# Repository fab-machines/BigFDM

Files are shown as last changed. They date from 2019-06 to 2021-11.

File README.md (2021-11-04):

<div align="center"><h1 style="font-family: courier;" align="center">BigFDM</h1></div>

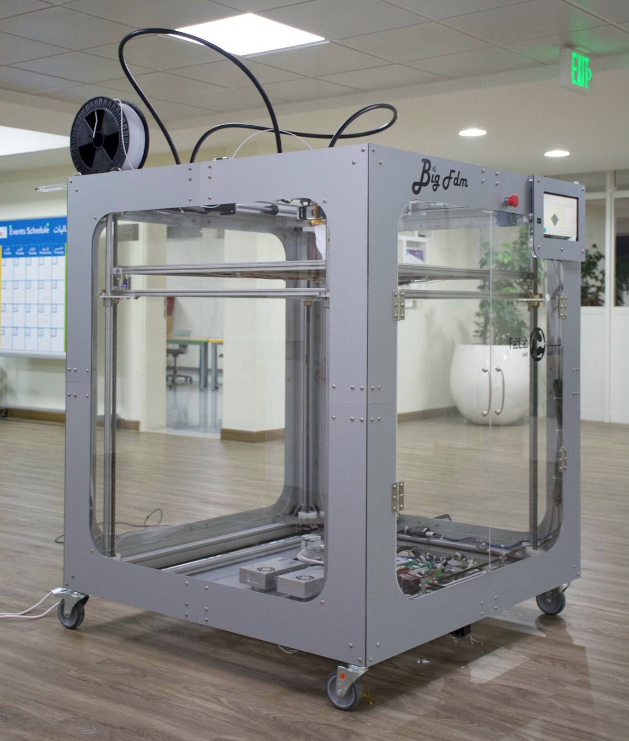
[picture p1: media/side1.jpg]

<div align="center"><i>Open Source Large Scale 3D Printer</i></div>

Premises
--
We dream in a future of freedom, where open source hardware and [Fab Labs](https://fablabs.io/) enable people to fully understand how to make things they need, and where decentralized local production is customized to impact the surrounding community. Believing that empowering the user with knowledge about how to make machines, BigFDM wants to give to the world a powerful open source tool, to 3D print any large scale object you may need. And, together with [LaserDuo](http://laserduo.com/), this is one of the first steps in developing other machines sharing the same philosophy.

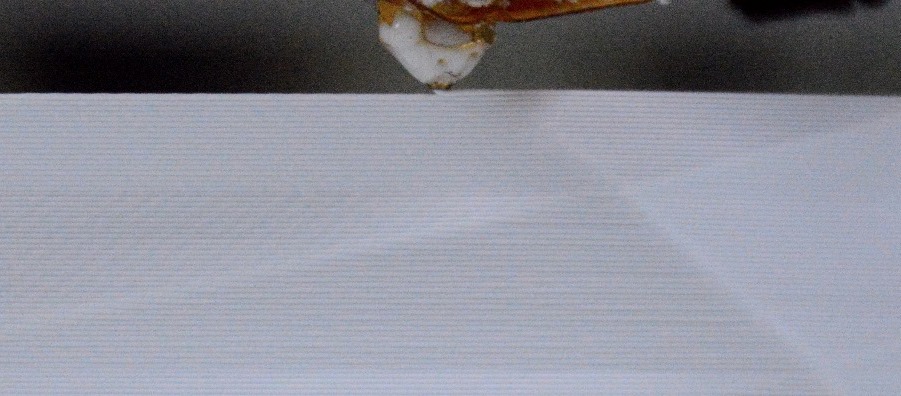
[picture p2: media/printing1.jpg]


BigFDM
--
BigFDM is an open source large scale 3D printer. 

Taking advantage of what we have learned in [Fab Academy](https://fabacademy.org/), BigFDM has been developed using standard [Fab Lab equipment](https://docs.google.com/spreadsheets/d/1U-jcBWOJEjBT5A0N84IUubtcHKMEMtndQPLCkZCkVsU/pub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) and [techniques](http://fab.academany.org/2019/schedule.html). BigFDM was in fact built in [Fab Lab UAE](http://fablabuae.ae/) by Daniele Ingrassia with the help of Hashim Al Sakkaf. Reversing the consumer process, where knowledge and building of machines stays inside a black box managed by companies, BigFDM brings the advantages of an open source development:

- full awareness about how the machine works
- reproducible design
- possibility to customize the machine and/or to build new ones
- built as much as possible with local materials
- local self-fixing and self-production of the machine parts
- community can use and improve the design
- cheap alternative to large scale 3D printers
- use BigFDM as tool to produce other open source machines

BigFDM allows the printing of large scale objects, some examples can be orthotics and prosthesis, art installations, furniture, replacement parts, industrial design prototypes, molds for casting of full scale parts. Using  Fused Deposition Modeling (or FDM), it can use standard 2.85mm 3D printer filament, and as well common extruders nozzles.

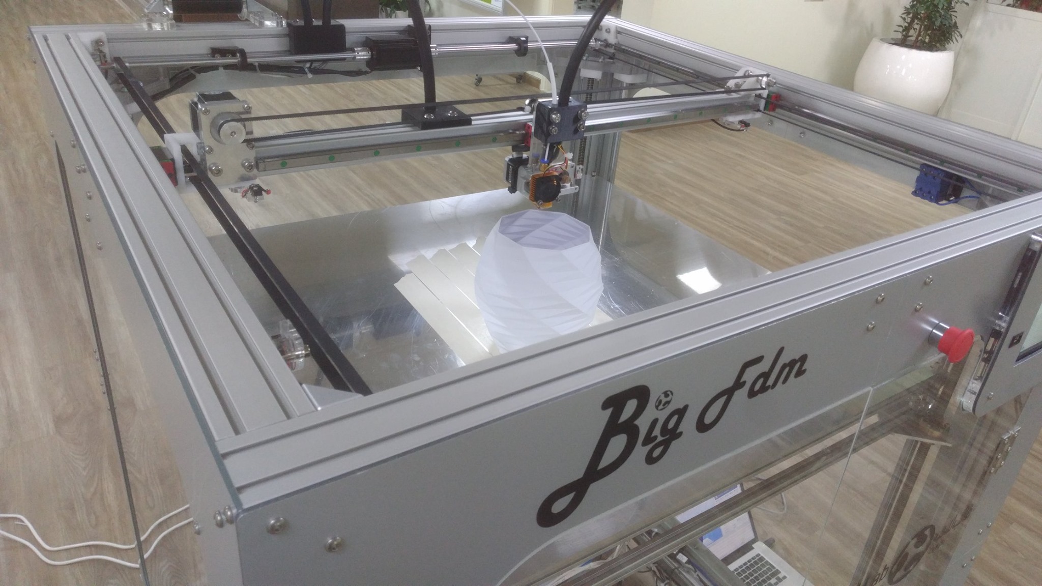
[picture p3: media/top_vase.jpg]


**BigFDM specifications**:

- **800mm x 800mm x 900mm** printing area
- **dual extruder** with interchangeble nozzle
- **2.85mm** filament
- **0.4 - 1mm** nozzle size
- **NEMA 24/23**  stepper motors
- stages with **HiWin linear guides**
- anodized **aluminium frame**
- **heated bed** with 4 x 750W bed heaters
- **closed housing** of aluminum composite and acrylic
- fabbable **[satshakit](https://github.com/satshakit) and [satstep](https://github.com/satstep)** based electronics
- **integrated tablet** for machine control
- printing from **USB** drive
- BOM cost of about **2600€**
- power requirements 220V, 3000W max

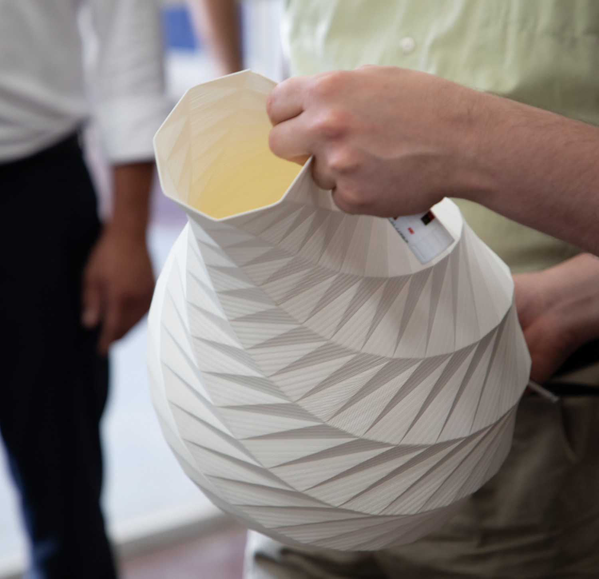
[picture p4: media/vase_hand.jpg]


Machine design
--
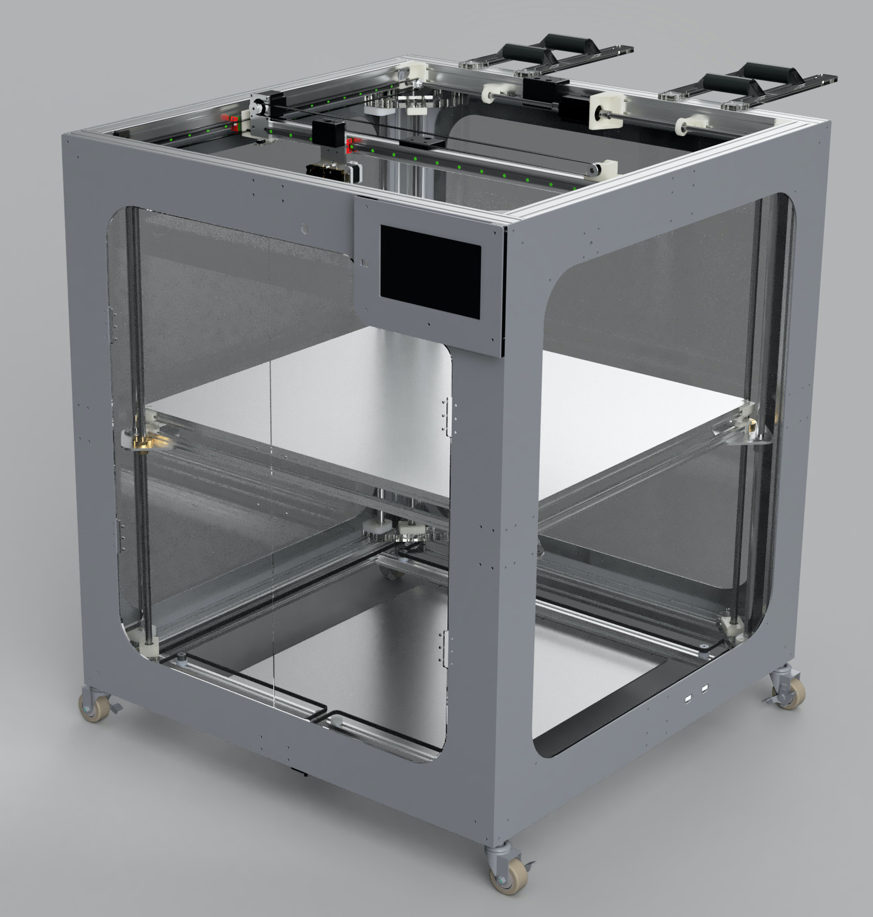
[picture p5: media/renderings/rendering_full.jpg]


BigFDM has been designed considering to keep fixed from the beginning few constraints, which then influenced the rest of the subsequent design choices:

- the all machine parts must be inside a boxed main frame
- the machine XY stages design must be independent and consistent by itself
- the Z axis moves the bed up or down

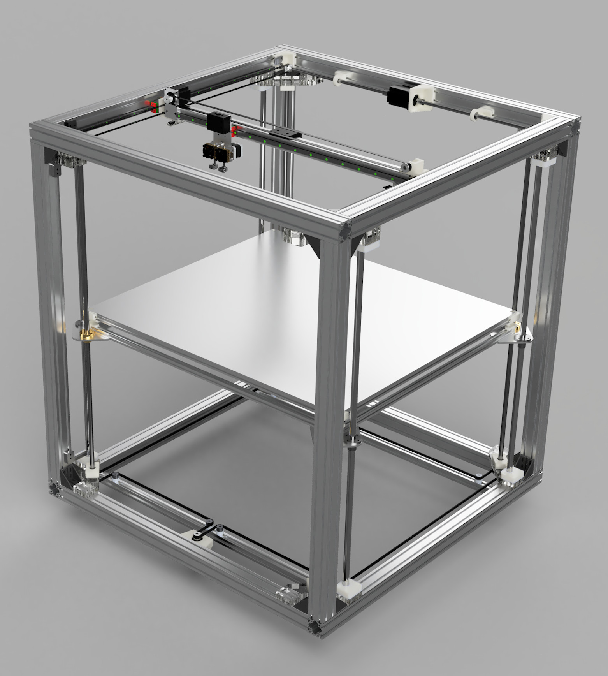
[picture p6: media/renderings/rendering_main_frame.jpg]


These have been tought in order to bring the following benefits:

- a **compact design** that maximize the printing area while minizing the unused space (just 2mm between the bed supports and the housing!)
-  minimizing the unused space has **lowered the cost** of the frame and the housing parts
-  the main frame serves both as **structural squared reference** for all the machine parts and well as body for the housing
-  the **XY stages can be completely removed** without disassembling any other machine section
-  the **XY stage indipendent design** can be reused to develop other machines
-  the machine printing **area can be scaled up/down** just by changing the length of few machine parts

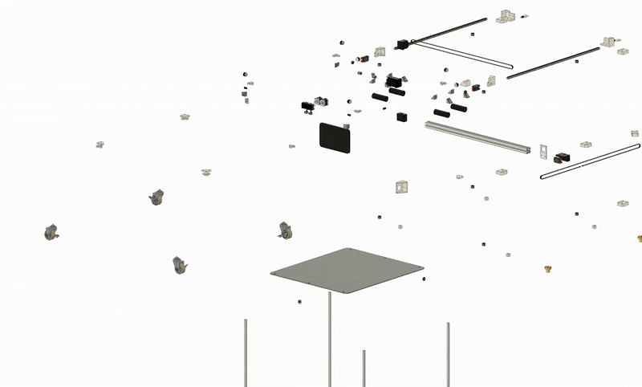
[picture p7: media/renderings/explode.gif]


X and Y stages
--
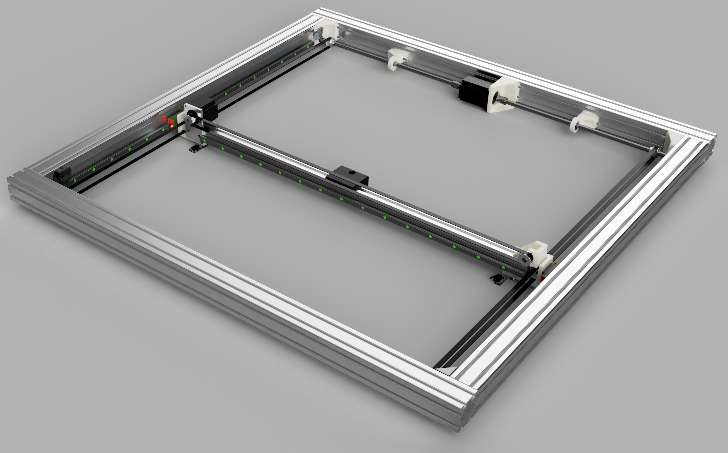
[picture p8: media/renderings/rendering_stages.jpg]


The X and Y stages integrates all their components inside a squared plane frame of T-Slots profiles. Hiwin 15mm linear guides and 10mm GT2 belts, together with custom CNC milled POM parts have been used. Implementing a sort of **stages interoperability**, the stages frame can be completely detached from the machine, and virtually, plugged into a different machine having similar frame shape (eg a laser cutter). Similar interoperability has also been recursively kept for the Y axis, which can be modified/removed without changing the X axis. 

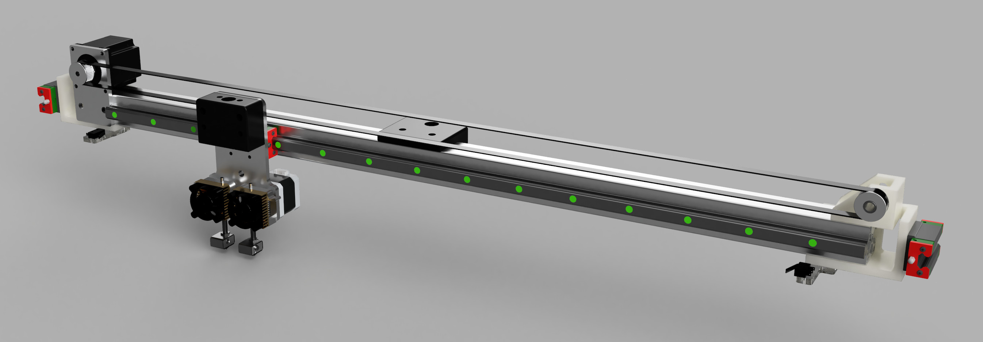
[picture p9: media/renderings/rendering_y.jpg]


Z axis
--

The Z axis uses a single NEMA 24 to move 4 lead screws guided by 4 linear rods and bearings. A 4.7m closed loop HTD M3 belt is used to transmit the movement with a 2 to 1 pulley ratio. The lead screws are supported by ball bearing both at the top and the bottom, where also pulleys are attached. The corner structural parts are made with CNC milled 20mm acrylic, while the rods and bearing supports use CNC milled POM. Because of layer by layer downwards needed movements, the bed will never move fast, with the maximum speed used more for manual movements. The main frame is used as support structure for all the Z axis parts.

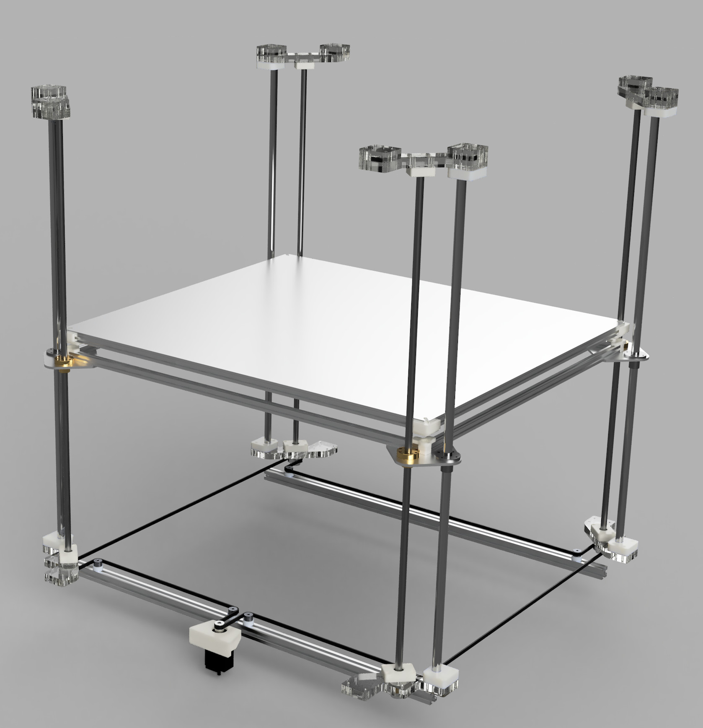
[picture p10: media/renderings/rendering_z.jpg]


Bed
--

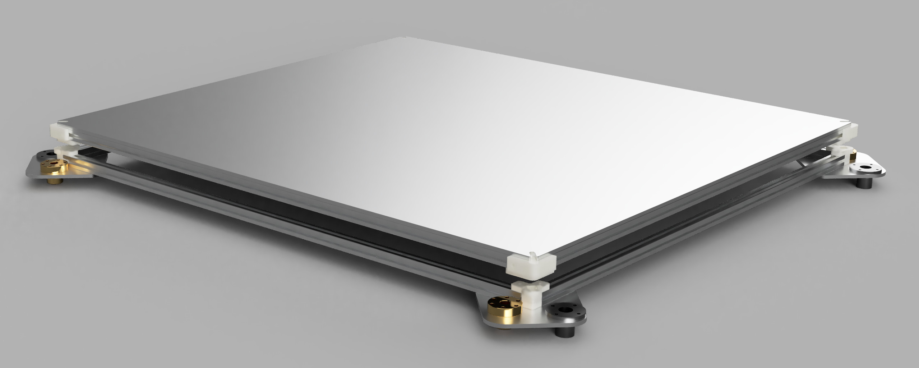
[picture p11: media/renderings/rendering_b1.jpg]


Made out of a 6mm aluminum plate cut with the CNC, the printing bed is suspended onto a lower frame structure by using 4 x 8mm DIN 912 bolts. The lower bed frame in turn is attached to the Z axis lead screws and linear rods. The lower frame is kept parallel to the upper stages by mechanically aligning it during the assembly, while the printing bed flatness can be finely tuned by screwing/unscrewing the 4 bolts. The design of the printing bed takes into account its **thermal expansion**, leaving a tolerance of expansion that exceeds the calculated one from the aluminum.

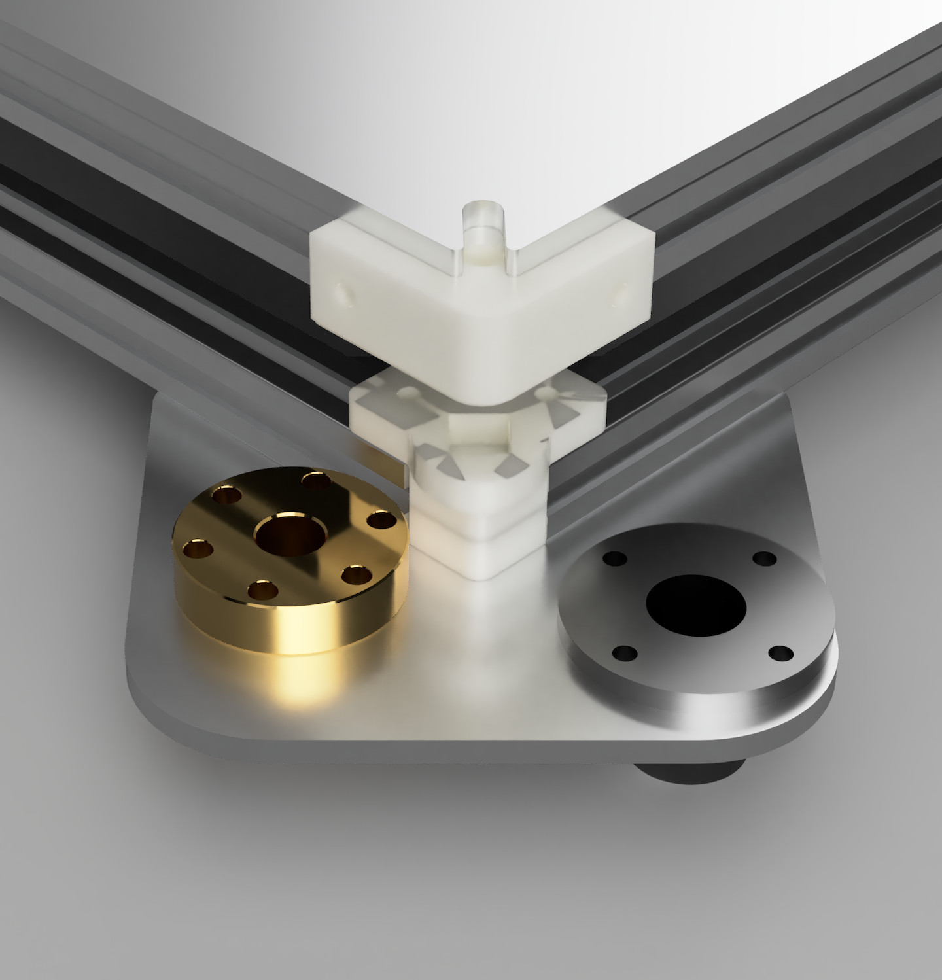
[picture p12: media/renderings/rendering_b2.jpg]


Housing
--

The housing has been developed to keep the internal temperature stable, and to allow the bed to quickly warmup. Because the machine parts have been constrained to be inside, the housing is attached directly to the main frame, and no additional parts are needed. The corners are made by 4mm aluminum composite (also called as dibond), while the windows are 6mm acryllic. Both materials have been CNC milled and the design is made in a way to fit two full sheets (about 2400x1250mm) of acrylic and one of aluminum composite. The tablet enclousure is made with the same materials, and allows to quickly remove it from the top.

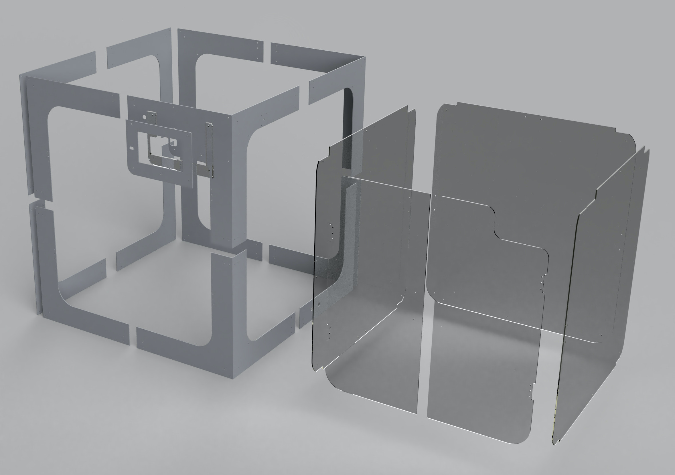
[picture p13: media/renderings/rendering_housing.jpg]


Electronics
--
The electronics of BigFDM consists of a set of fabbable electronics, derived from the original **[satshakit](https://github.com/satshakit)** board and **[satstep](https://github.com/satstep)** stepper drivers, plus some additional boards. Following the used boards and their role in BigFDM.<br>

**[satshakit-mega](https://github.com/fab-machines/BigFDM/tree/master/electronics/satshakit-mega)**

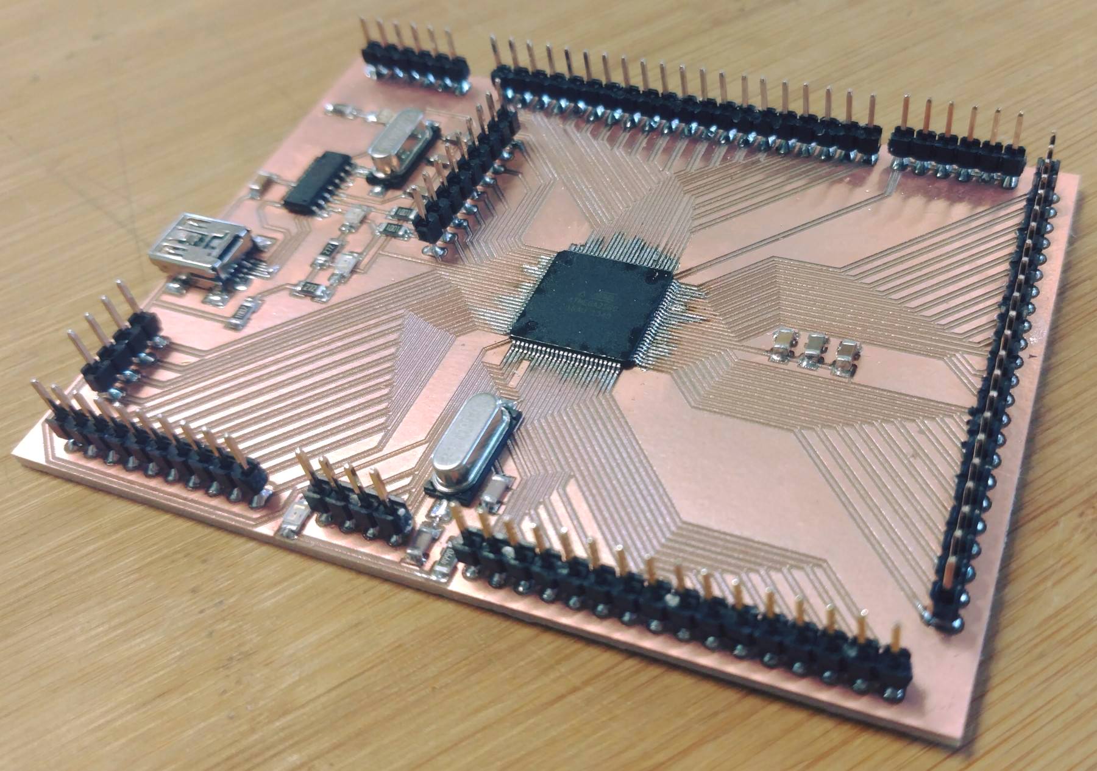
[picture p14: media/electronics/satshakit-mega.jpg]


Based on the [ATMega2560](https://www.microchip.com/wwwproducts/en/ATmega2560), this board provides the necessary microcontroller hardware for the Marlin manage its logic functionalities. Furthermore integrates an USB-to-Serial converter and USB port. Developed as general purpose board, not all the pins will be used. In the future this board will be a custom made solution for BigFDM. Link to the original [repo](https://github.com/satshakit/satshakit-mega).

---------

**[satstep6600](https://github.com/fab-machines/BigFDM/tree/master/electronics/satstep6600)**

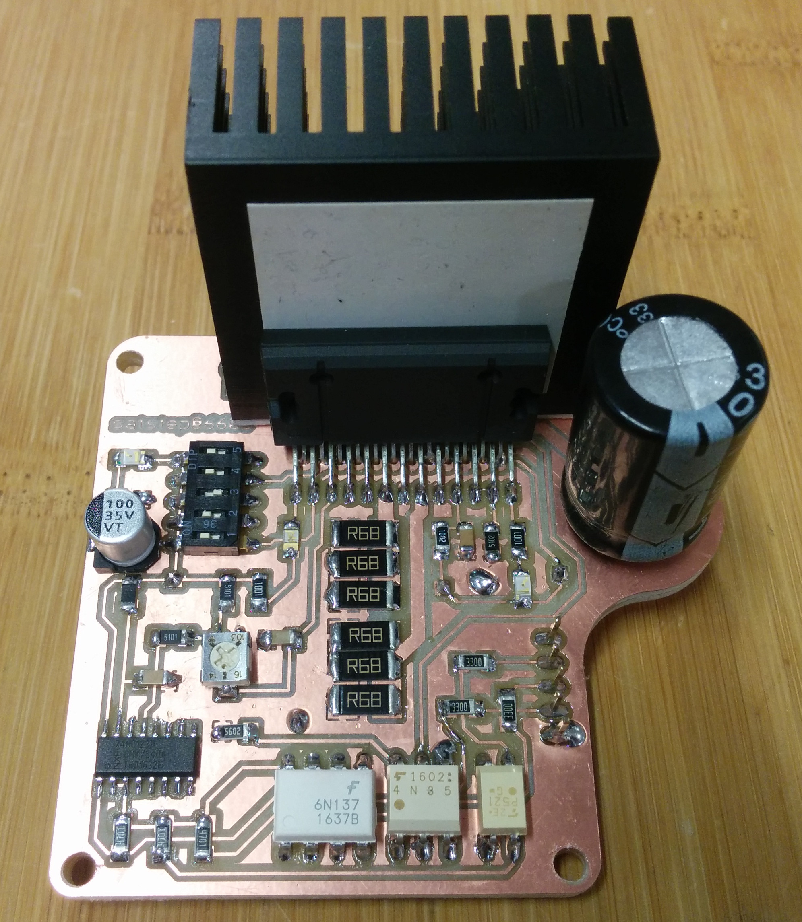
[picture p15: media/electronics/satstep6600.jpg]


Proved to have a robust design by being used in **[LaserDuo](http://laserduo.com/)** for more than a year, the satstep6600 is the stepper driver used to move the NEMA 23/24 used in BigFDM. Based on the Toshiba [TB6600HG](http://www.massmind.org/images/massmind/TB6600HG_datasheet.pdf) it can give up to 4.5A per coil to a single motor, whereas the NEMA 24 used will take a maximum of 4A. Link to the original [repo](https://github.com/satstep/satstep6600).

---------

**[Mosftet Board](https://github.com/fab-machines/BigFDM/tree/master/electronics/mosfet-board)**

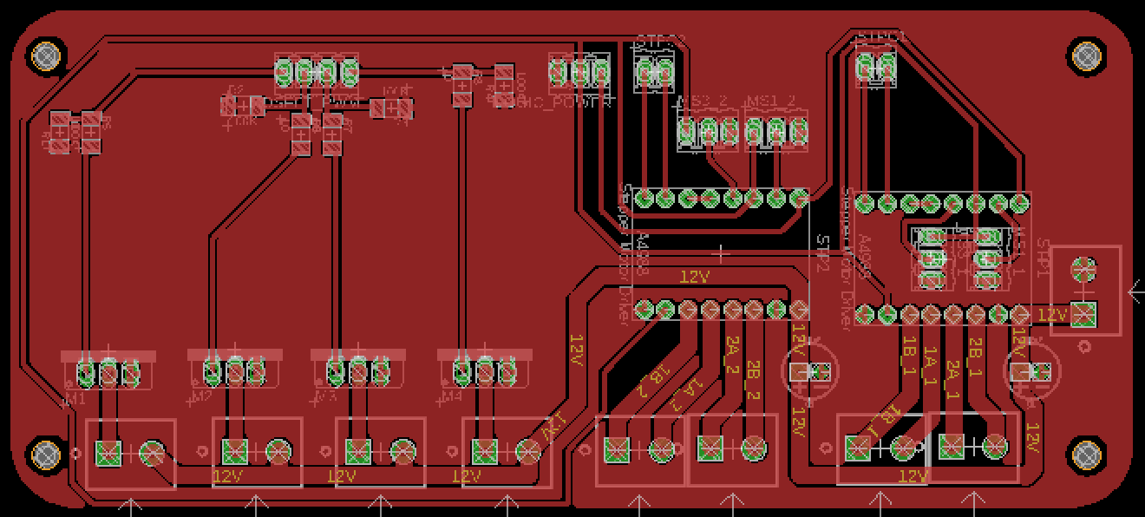
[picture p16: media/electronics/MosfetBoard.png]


Developed as an add-in to the satshakit-mega for BigFDM, the mosfet board integrates 4 mosfets to drive the nozzle heaters and the solid stae relay for the bed heaters, plus two slots for Pololu A4988 or similar stepper drivers. The A4988 are used to drive the two nozzle stepper motors.

---------

**[Sensor Board](https://github.com/fab-machines/BigFDM/tree/master/electronics/sensor-board)**

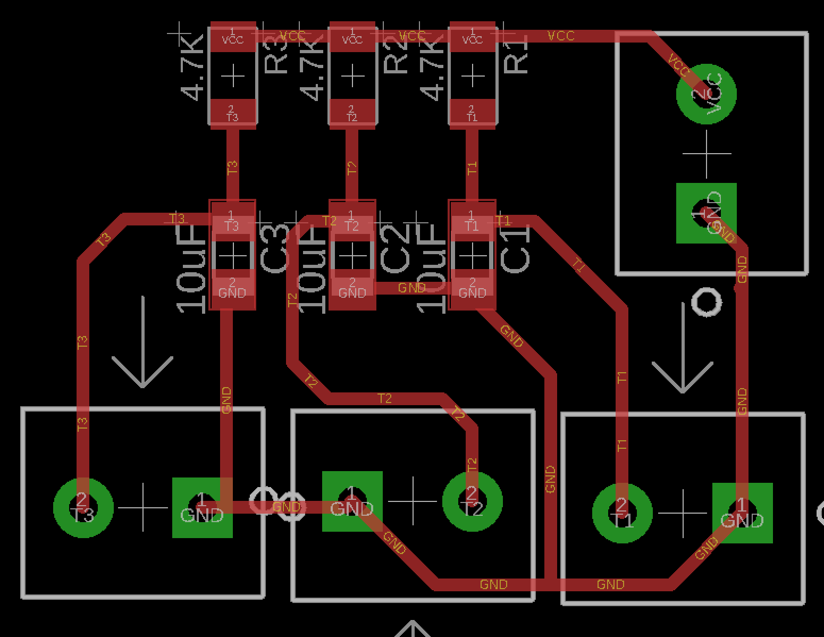
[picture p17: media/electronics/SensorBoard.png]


The sensor board integrates simple design with filtering capacitors and pull-up resistor. To this board the thermistors from the extruder and one of the thermistor of the bed heaters will be connected, together with the analog pins from the satshakit-mega.

---------

**[Endstop Board](https://github.com/fab-machines/BigFDM/tree/master/electronics/endstop-board)**

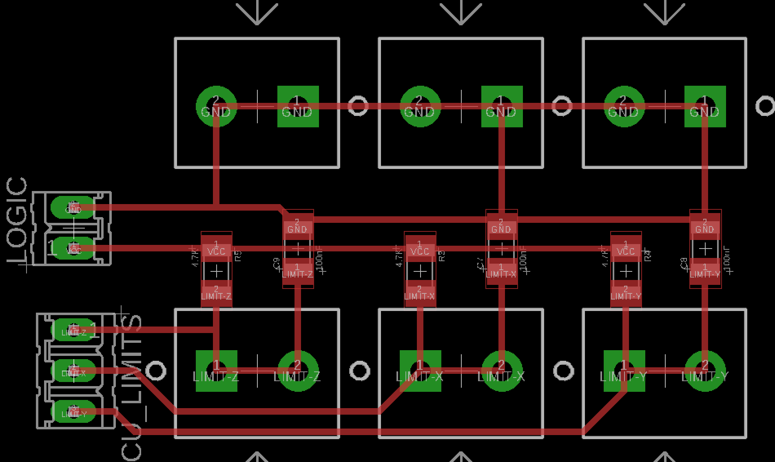
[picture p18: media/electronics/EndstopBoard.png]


In a similar way of the Sensor Board, the Endstop Boards has some pull-up resistors and some capacitors to filter the noise coming from the endstops. To this board the endstops and the limits min (x-min, y-min, z-min) from the satshakit-mega will be connected. BigFDM uses normally open endstops. 

---------

Summary of the needed boards:

- 1 x satshakit-mega
- 3 x satstep6600
- 1 x mosfet board
- 1 x endstop board
- 1 x sensor board

To power all this electronics, and to switch on and off the heaters the following additonal parts are needed:

- 15A 24V power supply
- 25A 12V power supply
- 25A 230V solid state relay
- 3 x 24V fans (for the 3 x satstep6600)

Software
--
BigFDM uses **[Marlin firmware](https://github.com/MarlinFirmware/Marlin)** running on the satshakit-mega. The configuration changes have been applied into the configuration.h file, you can find it in the [config](https://github.com/fab-machines/BigFDM/tree/master/config) folder of this repository.

To control the machine and to stream the G-Code, [Repetier-Host](https://www.repetier.com/) has been used.

Build your own BigFDM
--

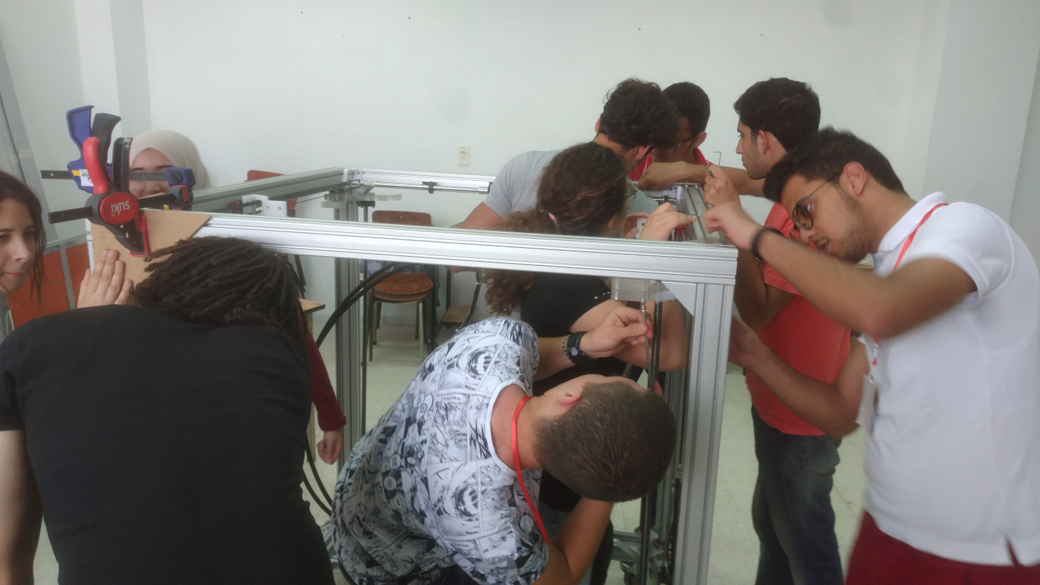
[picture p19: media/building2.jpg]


BigFDM is made by using a mix of fabricated and ready-made parts. The ready-made parts are selected to be as common/standard as possible, to make the sourcing of them easy in many countries. For both the raw materials needed for the fabricated parts, and the ready-made parts, refer to the Bill-of-Material for details: **[BigFDM BOM](https://github.com/fab-machines/BigFDM/raw/master/docs/BigFDM%20BOM.pdf)**

The fabrication of the parts mainly relays on standard [Fab Lab equipment](https://docs.google.com/spreadsheets/d/1U-jcBWOJEjBT5A0N84IUubtcHKMEMtndQPLCkZCkVsU/pub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). It will be therefore possible to make BigFDM in any of Fab Labs worldwide having it. Below a list of the required tools and machines:

- C02 laser cutter:
 - able to cut 8mm acrylic
 - needed for small acrylic parts
- large format wood CNC machine:
 - ShopBot or similar, size 2500x1250mm
 - to machine the aluminum parts (bed, Z axis supports)
 - to machine the aluminum composite for the housing
 - to machine the acrylic for the housing windows
 - to machine the POM parts (motor holders, attachments)
- 3D printer:
 - a small one (20x20x20cm) is sufficient
 - to print the filament/cables holders 
- Desktop format CNC machine:
 - Roland MDX50/MDX20/SRM20 or similar small machine (as well the cheap chinese ones)
 - to produce the required PCBs
- standard set of tools:
 - spanner key set
 - hex key set
 - DIN 875
 - calipers
 - rulers
 - screwdriver set
 - player set (grabber/cutter etc..)
 - clamps
 - rubber hummers

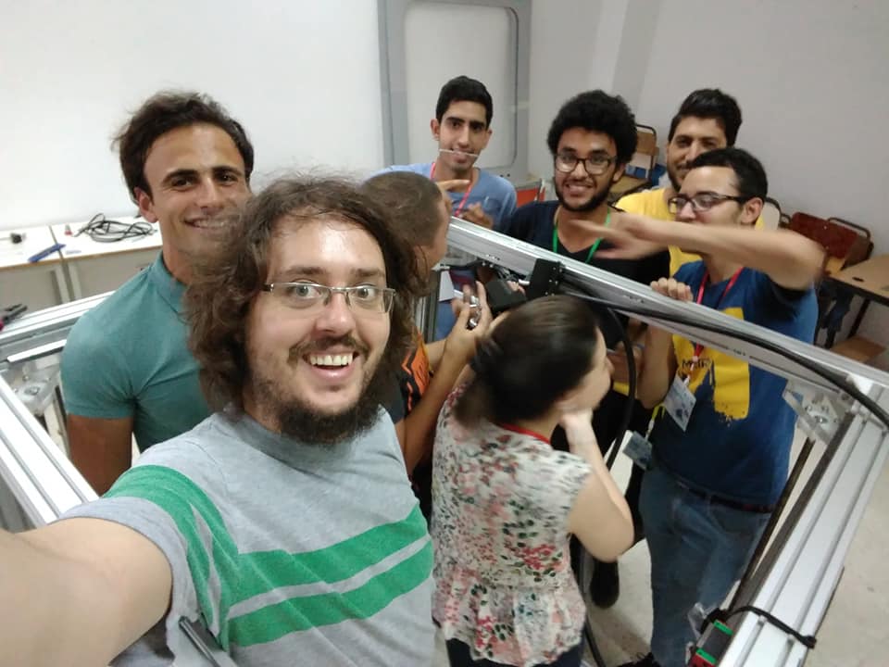
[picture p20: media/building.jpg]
 

Both fabricated and ready-made parts have been modeled inside the **[BigFDM Fusion 360 model](https://github.com/fab-machines/BigFDM/raw/master/cad/BigFDM.f3d)**. Using Fusion is possible to export/prepare the parts for production in the following ways:

- right click save as STL, on a body that needs to be 3D printed
- use the built-in Fusion CAM processor for the machined parts
- project on a surface, and then right click export as DXF, for laser cutting
 
For more details about the tools and once you have all the fabricated and ready-made parts parts available, refer to the for step-by-step assembly instructions and tips: **[BigFDM Building Manual](https://github.com/fab-machines/BigFDM/wiki/Big-FDM-Building-Manual)** 

Big FDM requires different fabbable PCBs to work. Below the download links for the eagle files that you use to fabricate them:

- **[satshakit-mega schematic](https://raw.githubusercontent.com/fab-machines/BigFDM/master/electronics/satshakit-mega/satshakit-mega.sch)**, **[satshakit-mega board](https://raw.githubusercontent.com/fab-machines/BigFDM/master/electronics/satshakit-mega/satshakit-mega.brd)**
- **[satstep6600 schematic](https://github.com/fab-machines/BigFDM/raw/master/electronics/satstep6600/satstep6600.sch)**, **[satstep6600 board](https://github.com/fab-machines/BigFDM/raw/master/electronics/satstep6600/satstep6600.brd)**
- **[mosfet board schematic](https://github.com/fab-machines/BigFDM/raw/master/electronics/mosfet-board/mosfer-board.sch)**, **[mosfet board](https://github.com/fab-machines/BigFDM/raw/master/electronics/mosfet-board/mosfet-board.brd)**
- **[sensor board schematic](https://github.com/fab-machines/BigFDM/raw/master/electronics/sensor-board/sensor-board.sch)**, **[sensor board](https://github.com/fab-machines/BigFDM/raw/master/electronics/sensor-board/sensor-board.brd)**
- **[endstop board schematic](https://github.com/fab-machines/BigFDM/raw/master/electronics/endstop-board/endstop-board.sch)**, **[endstop board](https://github.com/fab-machines/BigFDM/raw/master/electronics/endstop-board/endstop-board.brd)**

Download here the configuration files (right click save as):

- **[Marlin BigFDM](https://github.com/fab-machines/BigFDM/raw/master/config/Marlin-1.1.x-BIGFDM.zip)** 
- **[Cura profile settings for 1mm nozzle](https://github.com/fab-machines/BigFDM/raw/master/config/Cura_BigFDM.curaprofile)** 
- **[Cura  machine settings](https://github.com/fab-machines/BigFDM/raw/master/config/BigFDM_machine_settings.png)**
- **[Cura extruder settings](https://github.com/fab-machines/BigFDM/raw/master/config/BigFDM_extruder_settings.png)**

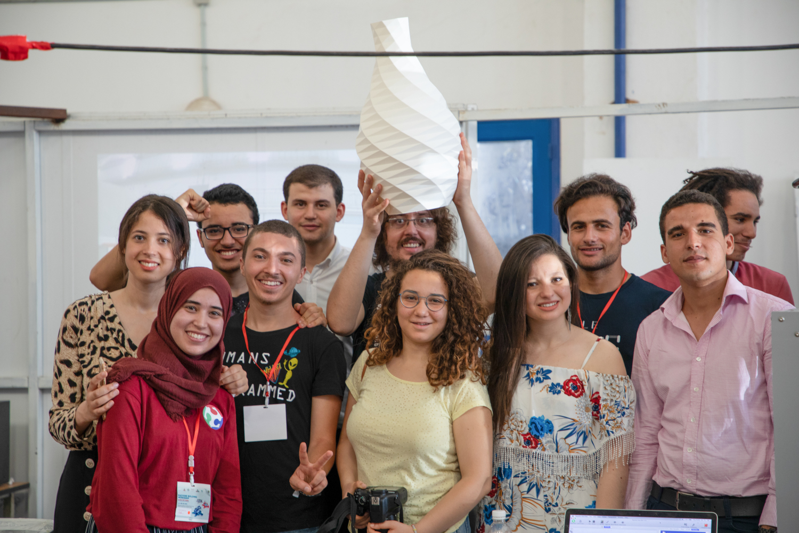
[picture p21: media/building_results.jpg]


Known issues
--

- the extruder used is a dual Geetech MK8, which is good up to 0.5mm nozzle but has difficulties in keeping the temperature with an 1mm nozzle; in the future will be replaced by a custom made extruder supporting nozzles up to 2mm

- because of the difficulties for the extruder to warmup, to save time it is recommended to start heating it manually whenever possible before starting printing 

- the electronics setup requires improvements, especially a custom made board in place of the satshakit-mega and an additonal all-in-one board, replacing the mosfet, sensor and endstop boards

- the Z axis design needs multiple parts for the supporting corners of the lead screws and the linear rods; in the future replaced by an unique block of CNC milled aluminum

- the G-Code streaming from the tablet is sometimes gets corrupted and/or interrupts suddenly; is needed to use an higher quality shielded USB cable, or  to try Octoprint instead of Repetier host as G-Code streamer

Media
--
**BigFDM printing**

<a href="http://www.youtube.com/watch?feature=player_embedded&v=mlnE0L0cWro
" target="_blank"></a>

<a href="http://www.youtube.com/watch?feature=player_embedded&v=w7HM4-2B8Nc
" target="_blank"></a>

**How to Make BigFDM: Tunisia Workshop at [Fab Lab ENIT](https://www.facebook.com/FabLabENIT/)**

<a href="http://www.youtube.com/watch?feature=player_embedded&v=wLneWQhjYCM
" target="_blank"></a>

**BigFDM pictures**

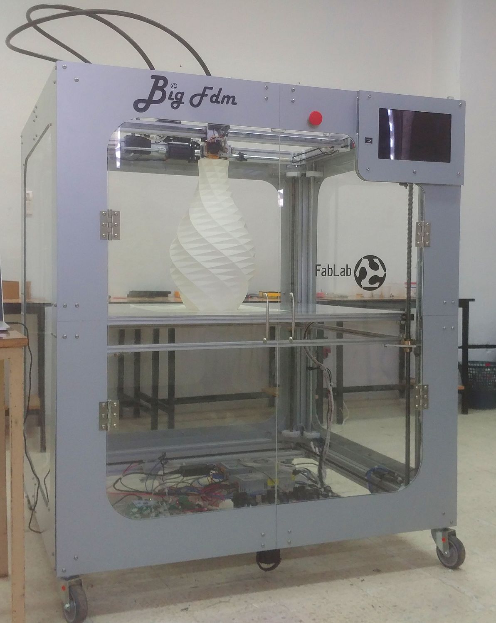
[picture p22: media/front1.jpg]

<br><br><br>
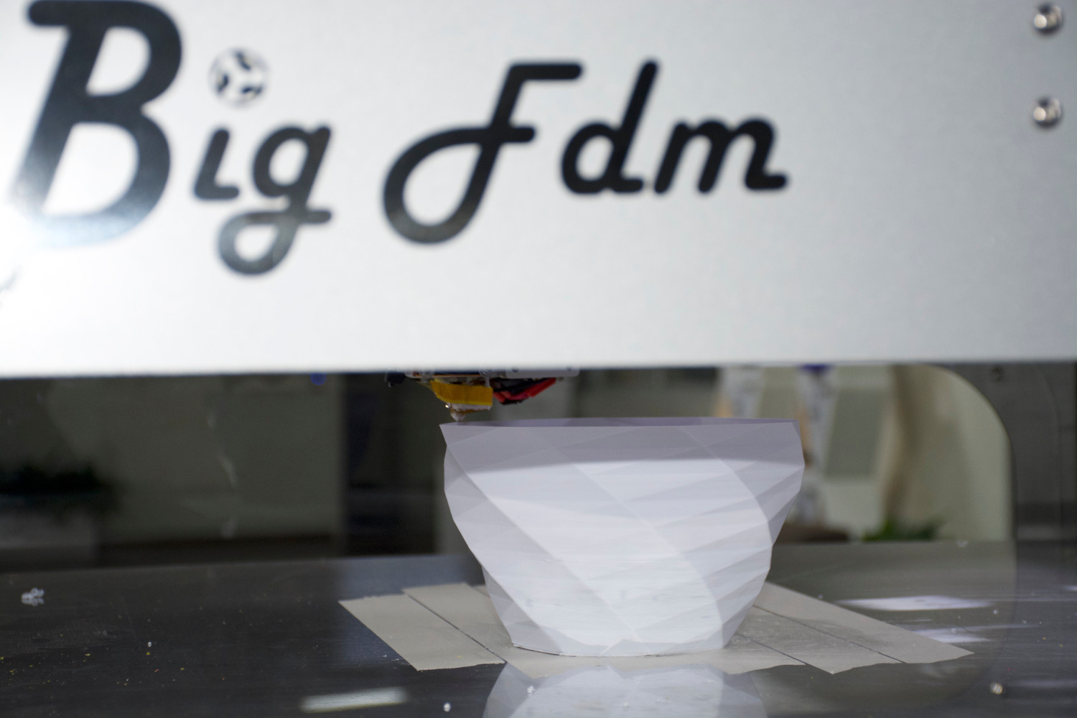
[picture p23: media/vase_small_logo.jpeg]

<br><br><br>
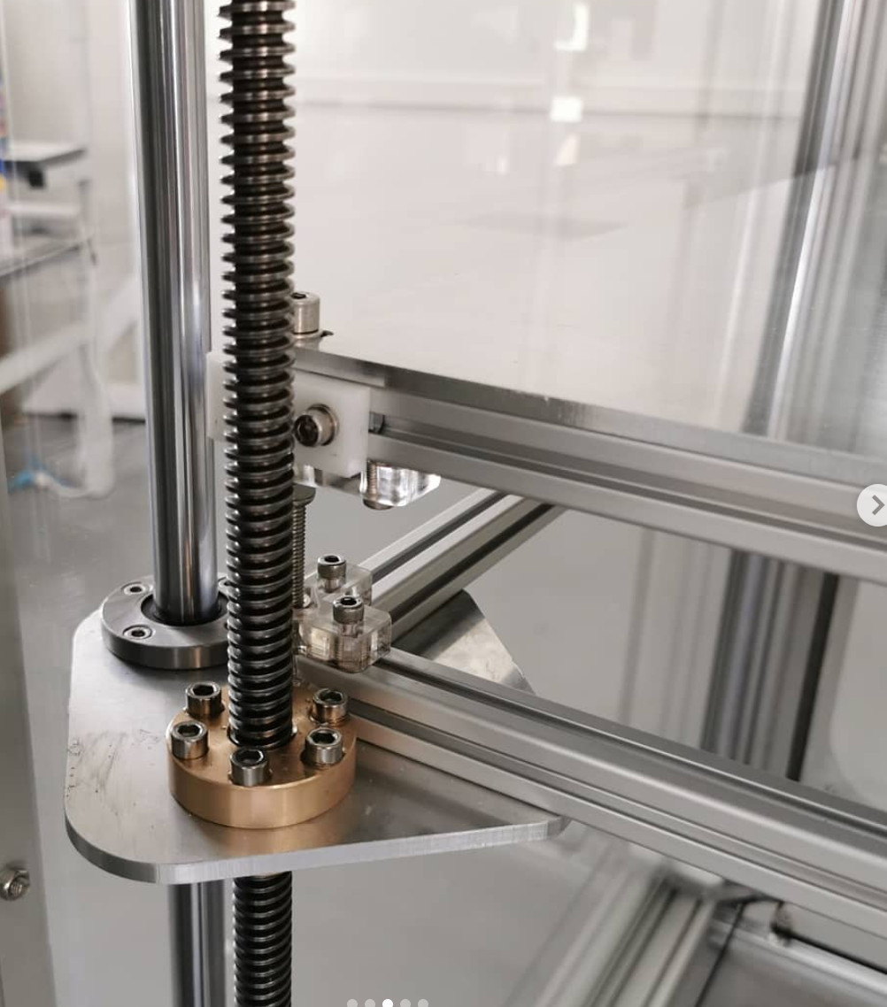
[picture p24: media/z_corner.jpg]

<br><br><br>
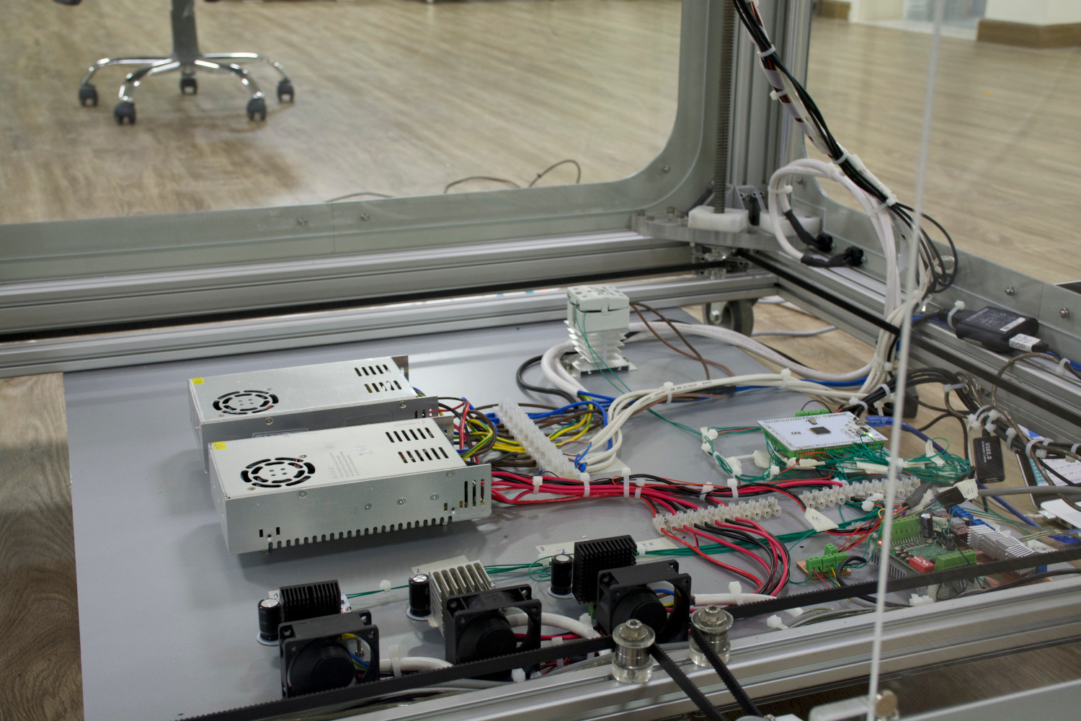
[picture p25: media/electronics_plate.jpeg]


Author
--

The author of BigFDM is:

- **Daniele Ingrassia, daniele@inmachines.net**
- **[InMachines Ingrassia GmbH](https://www.inmachines.net/)**

**Project Helper:**<br>
- **[Hashim Al Sakkaf](http://archive.fabacademy.org/fabacademy2017/fablabuae/students/154/)**

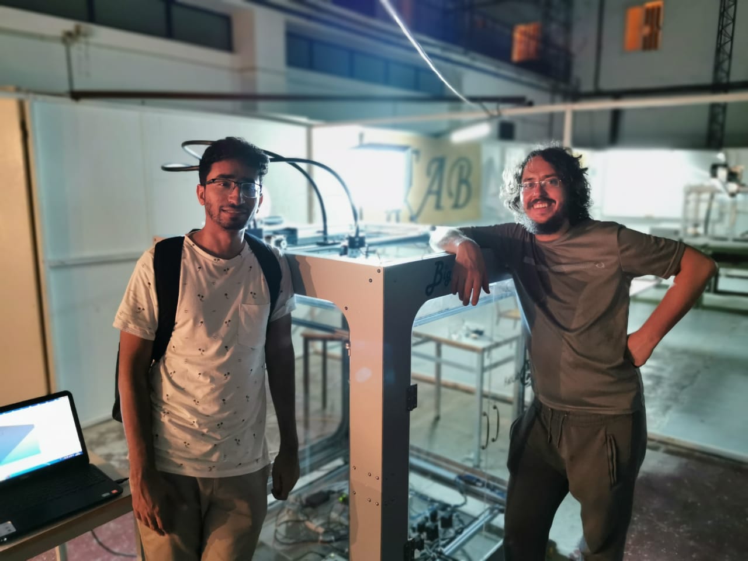
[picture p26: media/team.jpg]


Donations
--

Our dream is to have impact by making **open source machines digitally available and locally produced anywhere in world**. We plan to open a dedicated Fab Lab to foster open machine building and digital fabrication research. Practically several tasks and many expensens have to be sustained to give this dream the chance to have a future. Such as the renting of a proper space, the making/purchasing of proper equipment, the sustainability of our work and lifes. If you share this mindset and BigFDM is useful to you, please help us to make this dream a reality by donating your support:



Acknowledgements
--

The development of this machine has been funded by:<br>
**[German Federal Ministry of Education and Research](https://www.bmbf.de/en/index.html)**

Funds implemented by:<br>
**[OpenLab Hamburg](http://openlab-hamburg.de/startpage/)**<br>
[Helmut-Schmidt-Universität Universität der Bundeswehr](https://www.hsu-hh.de/en/)<br>
Laboratorium Fertigungstechnik<br>
Holstenhofweg 85<br>
22043 Hamburg<br>

Thanks:<br>
<br>
**[Fablab UAE](http://fablabuae.ae/)**<br />
176 6 D St - Satwa <br />
Dubai - United Arab Emirates<br />
fablabuae@gmail.com

**Paul Anand**

License
-- 
The BigFDM, its hardware design, CAD, BOM, settings and relative files are are released under the following open source license:

- CERN Open Hardware Licence Version 2 Weakly Reciprocal - **[CERN-OHL-W](LICENSE_CERN_OHL_W_V2.txt)**

Note
--

This documentation will be continuously improved as soon there are updates and/or improvements on the machine.

Disclaimer  
--

<div class="align-justify">
This hardware/software is provided "as is", and you use the hardware/software at your own risk. Under no circumstances shall any author be liable for direct, indirect, special, incidental, or consequential damages resulting from the use, misuse, or inability to use this hardware/software, even if the authors have been advised of the possibility of such damages.</div>

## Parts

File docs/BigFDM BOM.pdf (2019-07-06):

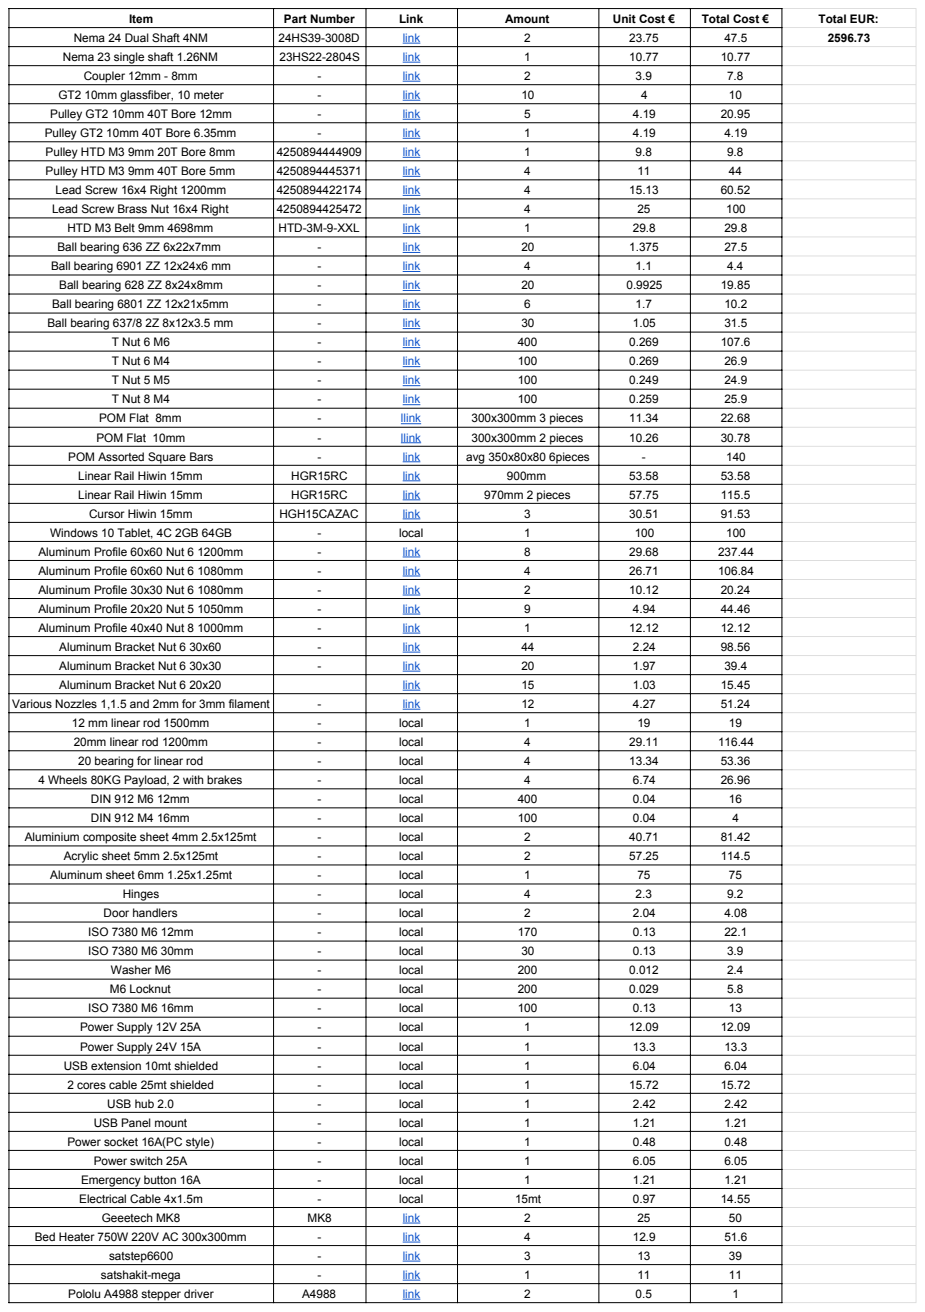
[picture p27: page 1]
Item; Part Number; Link; Amount; Unit Cost €; Total Cost €; Total EUR:; Nema 24 Dual Shaft 4NM; link

Nema 23 single shaft 1.26NM | 23HS22-2804S | link (https://www.omc-stepperonline.com/nema-23-bipolar-18deg-126nm-1784ozin-28a-25v-57x57x56mm-4-wires-23hs22-2804s.html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) | 1 | 10.77 | 10.77
Coupler 12mm - 8mm | - | link (https://www.ebay.de/itm/Wellenkupplung-flexibel-Alu-8mm-12mm-Industrie-CNC-RepRap-3D-Druck/162502682453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) | 2 | 3.9 | 7.8
GT2 10mm glassfiber, 10 meter | - | link (https://www.ebay.de/itm/172828639879) | 10 | 4 | 10
Pulley GT2 10mm 40T Bore 12mm | - | link (https://www.ebay.de/itm/162855300333?ViewItem=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) | 5 | 4.19 | 20.95
Pulley GT2 10mm 40T Bore 6.35mm | - | link (https://www.ebay.de/itm/162855300333?ViewItem=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) | 1 | 4.19 | 4.19
Pulley HTD M3 9mm 20T Bore 8mm | 4250894444909 | link (https://www.ebay.de/itm/Zahnriemenrad-HTD-3M-9mm-breit-20-Z%C3%A4hne-Bohrung-8mm-H7-mit-Klemmschrauben/273358648468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) | 1 | 9.8 | 9.8
Pulley HTD M3 9mm 40T Bore 5mm | 4250894445371 | link (https://www.ebay.de/itm/Zahnriemenrad-HTD-3M-9mm-breit-40-Z%C3%A4hne-Bohrung-5-00mm-H7-mit-Klemmschrauben/282406603683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) | 4 | 11 | 44
Lead Screw 16x4 Right 1200mm | 4250894422174 | link (https://www.ebay.de/itm/Trapezgewindespindel-RTS-TR-16X4-rechts-12-40-EUR-m-0-25-EUR-pro-Schnitt/273445369350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) | 4 | 15.13 | 60.52
Lead Screw Brass Nut 16x4 Right | 4250894425472 | link (https://www.ebay.de/itm/Trapezgewindemutter-Flansch-EBFM-16x4-rechts-Rotguss/282862793666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) | 4 | 25 | 100
HTD M3 Belt 9mm 4698mm | HTD-3M-9-XXL | link (https://www.ebay.de/itm/Zahnriemen-geschlossen-HTD-3M-Breite-9mm-L%C3%A4nge-800mm-bis-5100mm/273379846711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) | 1 | 29.8 | 29.8
Ball bearing 636 ZZ 6x22x7mm | - | link (https://www.ebay.de/itm/10-Stk-IBU-Rillenkugellager-Miniatur-Kugellager-636-ZZ-2Z-6x22x7-mm/281378919587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) | 20 | 1.375 | 27.5
Ball bearing 6901 ZZ 12x24x6 mm | - | link (https://www.ebay.de/itm/4-Stk-IBU-Rillenkugellager-Kugellager-6901-ZZ-61901-2Z-12x24x6-mm/282745713025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) | 4 | 1.1 | 4.4
Ball bearing 628 ZZ 8x24x8mm | - | link (https://www.ebay.de/itm/IBU-Miniaturlager-Rillenkugellager-623-629-2RS-oder-ZZ-Kugellager/370988706143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) | 20 | 0.9925 | 19.85
Ball bearing 6801 ZZ 12x21x5mm | - | link (https://www.ebay.de/itm/2-Stk-IBU-Rillenkugellager-Kugellager-6801-ZZ-61801-2Z-12x21x5mm/372277639681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) | 6 | 1.7 | 10.2
Ball bearing 637/8 2Z 8x12x3.5 mm | - | link (https://www.ebay.de/itm/10-Stk-IBU-Miniatur-Kugellager-MR128-ZZ-Rillenkugellager-637-8-2Z-8x12x3-5-mm/372580773494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) | 30 | 1.05 | 31.5

T Nut 6 M6 | - | link (https://www.ebay.de/itm/100x-Nutenstein-6-St-Nut-6-Typ-I-mit-Steg-Federkugel-Stahl-verzinkt/251851672402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) | 400 | 0.269 | 107.6
T Nut 6 M4 | - | link (https://www.ebay.de/itm/100x-Nutenstein-6-St-Nut-6-Typ-I-mit-Steg-Federkugel-Stahl-verzinkt/251851672402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) | 100 | 0.269 | 26.9
T Nut 5 M5 | - | link (https://www.ebay.de/itm/100x-Nutenstein-5-St-Nut-5-Typ-I-mit-Steg-Federkugel-Stahl-verzinkt/261661352233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) | 100 | 0.249 | 24.9
T Nut 8 M4 | - | link (https://www.ebay.de/itm/100x-Nutenstein-V-8-St-Nut-8-Typ-I-mit-Steg-Federkugel-Stahl-verzinkt/251851806459) | 100 | 0.259 | 25.9
POM Flat 8mm | - | llink (https://www.ebay.de/itm/POM-C-Zuschnitt-Platte-Dicke-6-und-8mm-B-x-L-w%C3%A4hlbar-schwarz-wei%C3%9F-natur-Platten/263404958597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) | 300x300mm 3 pieces | 11.34 | 22.68
POM Flat 10mm | - | llink (https://www.ebay.de/itm/POM-C-Zuschnitt-Platte-Dicke-10-12-15-20-mm-BxL-w%C3%A4hlb-schwarz-wei%C3%9F-natur-Platten/263404960139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) | 300x300mm 2 pieces | 10.26 | 30.78
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

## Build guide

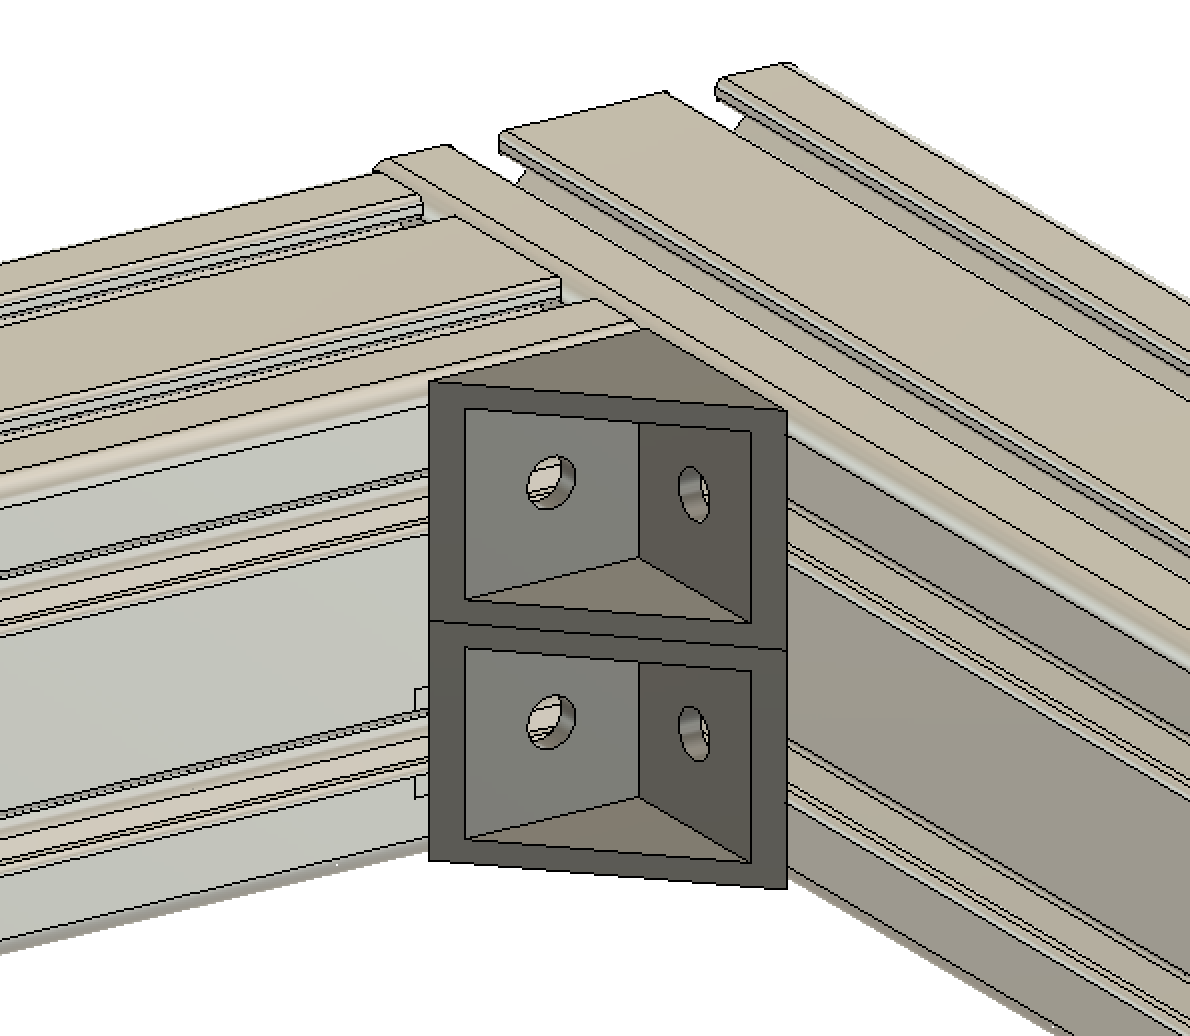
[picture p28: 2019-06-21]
media/building_manual/Step2_3.png

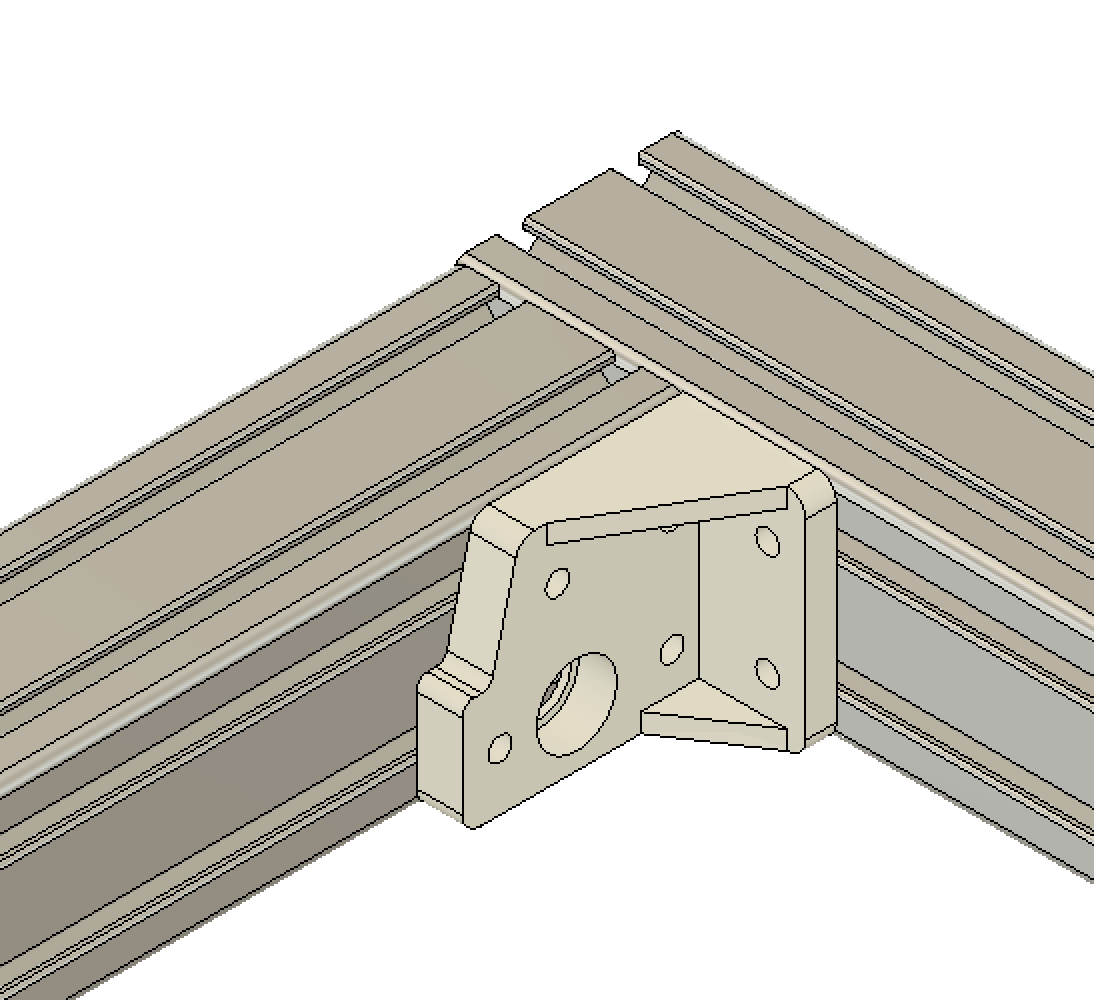
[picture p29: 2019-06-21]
media/building_manual/Step2_2.png

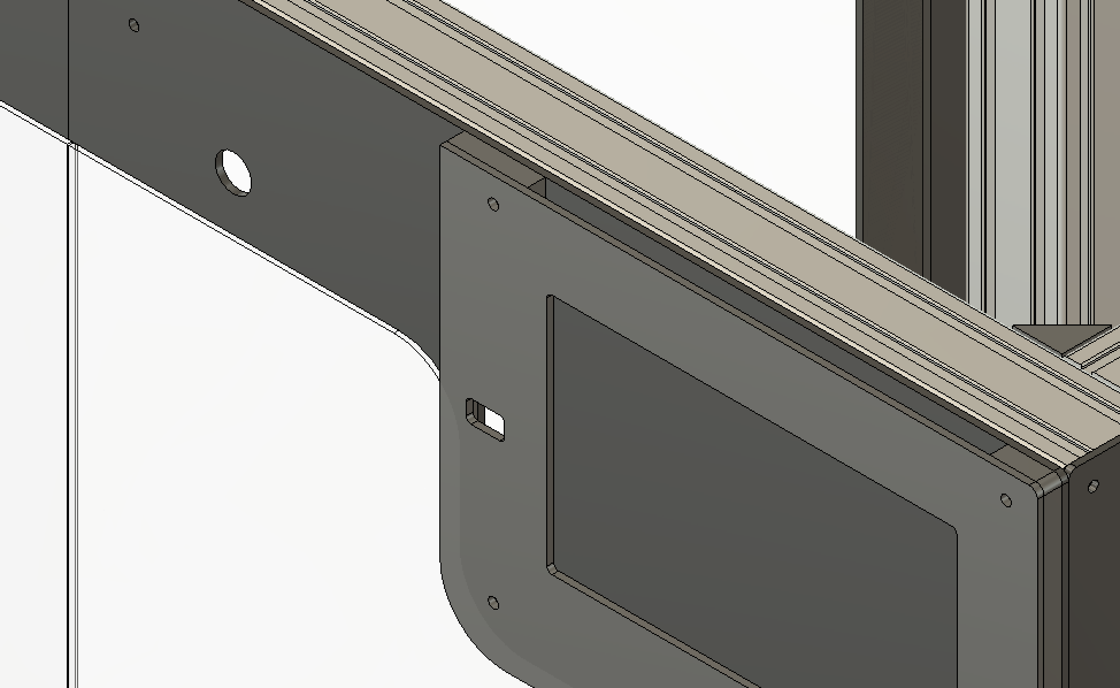
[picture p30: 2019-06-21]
media/building_manual/Step9_21.png

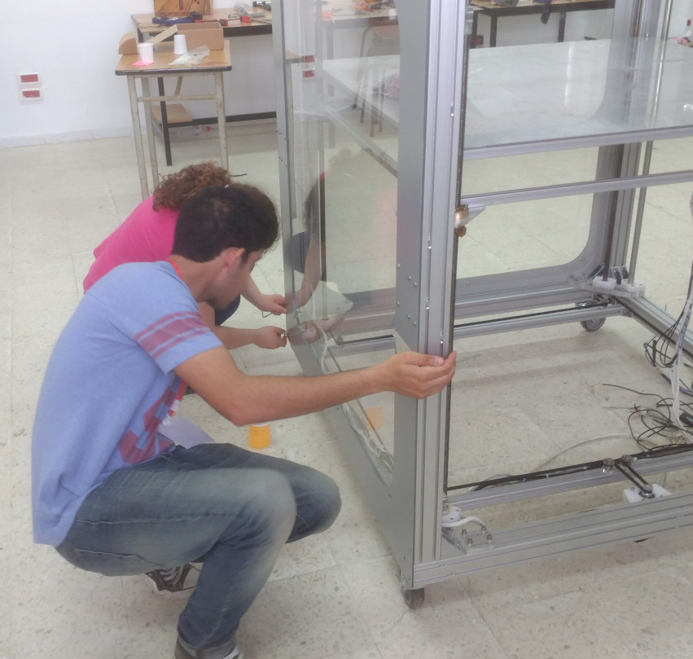
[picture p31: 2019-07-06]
media/building_manual/housing_installation.jpg

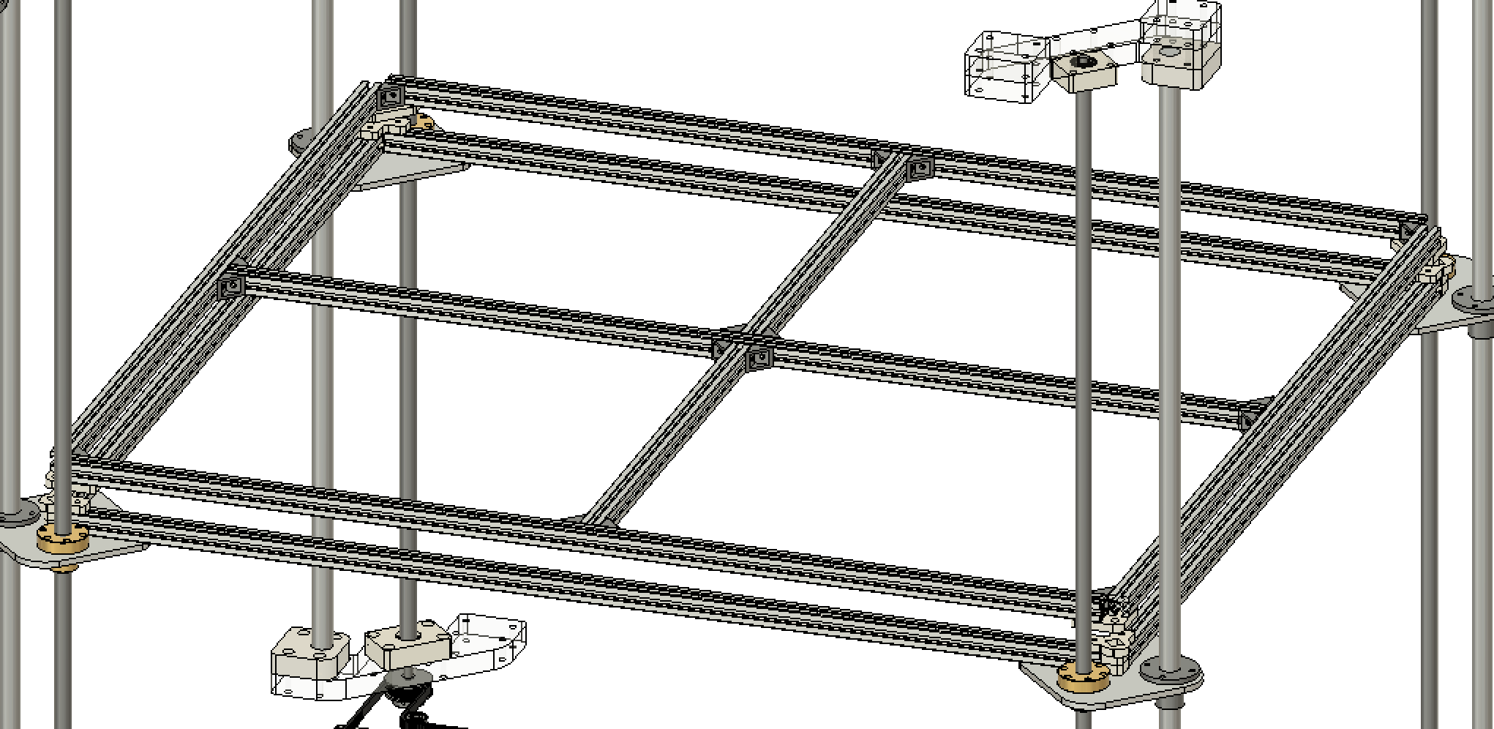
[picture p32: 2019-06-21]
media/building_manual/Step8_8.png

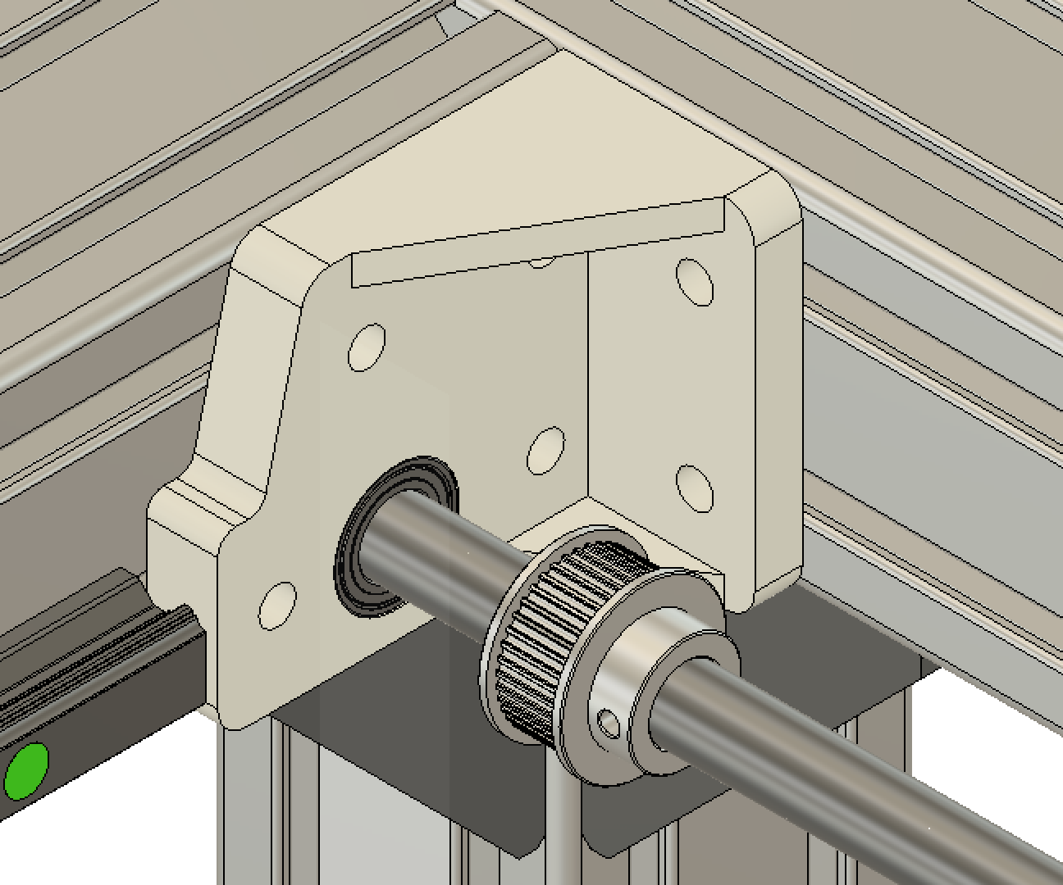
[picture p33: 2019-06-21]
media/building_manual/Step4_2.png

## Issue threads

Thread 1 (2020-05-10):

Add multi material upgrade

janknieling, 2020-05-10:
Hi,

I think it will be a very nice/useful feature to have a multi material upgrade kit like for the prusa i3/the possibility to print with multiple filaments/colours at the same time.

Maybe the MMU2 for the prusa i3 MK3S can be a good template...
https://shop.prusa3d.com/en/printer-upgrades/183-original-prusa-i3-mk3-multi-material-upgrade-kit.html

https://github.com/prusa3d/Original-Prusa-i3/tree/MMU2

satshas, 2021-08-30:
Hello,

sorry, this issue must have been missed!

You're absolutely right that with such big area multi material is a nice-to-have feature.
In the next version of the machine we will try implement something similar.

Thanks,
Daniele

Closed 2021-08-30.

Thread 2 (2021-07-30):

Any design update

ndkazu, 2021-07-30:
Hello,
I am planning to build this printer with some of my colleagues.
It would really be nice if you had some advice or design updates/improvements to suggest.
also, for the 3d model, is it possible to have a more common format? (igs, stp,etc.. )
cordially,
Kazunobu

satshas, 2021-08-30:
Hello,

a new version of the machine has been developed, overcoming many of the initial issues, and finally offering a cubic meter printing area.

We hope that by the end of this year we could start release some updates.

Stay tuned!

All the best,
Daniele

Closed 2021-08-30.

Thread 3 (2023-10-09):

Hardware usage

3dprintpittsburgh, 2023-10-09:
Working on building this up now and buying through the BOM. While looking at the BOM, there's requirements for:

 - T Nut 6mm slot m6 * 400
 - T Nut 6mm slot m4 * 100
 - T Nut 5mm slot m5 * 100
 - T Nut 8mm slot m4 * 100

The thing is, I'm having a hard time figuring out which areas technically use which hardware. Looking at the CAD model, no hardware is present, and the build manual makes no mention to hardware for each section that I can see.

Obviously, the 8mm slot is used for the X-axis, where there's a 4040 extrusion that has an 8mm slot. All of the frame rails and cross supporting members for the base plate and build plate all have 6mm slots. I'm assuming the m6 /6mm slot gets used to graft the frame and build plate together, and the 6mm slot / m4 is for attaching motors / accessories. Is this correct?

Also, I can't figure out where the 5mm slot / m5 hardware gets used at all. Looking around the CAD model, it looks like 6mm slot works everywhere.

Can someone please help point me in the right direction here?

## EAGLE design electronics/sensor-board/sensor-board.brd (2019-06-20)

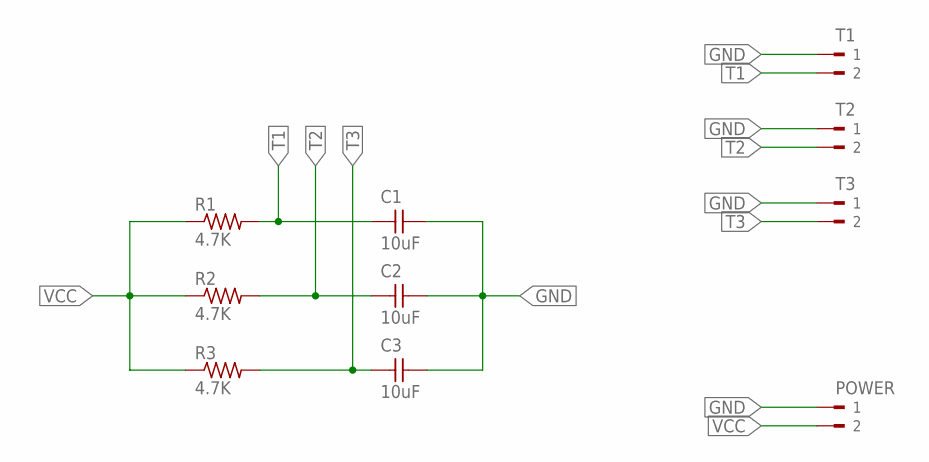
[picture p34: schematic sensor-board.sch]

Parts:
C1, C2, C3: 10uF; 1206
POWER: PM5.08/2/90BLK; WEIDMULLER_PM5.08_2
R1, R2, R3: 4.7K; R1206FAB
T1, T2, T3: PM5.08/2/90BLK; WEIDMULLER_PM5.08_2

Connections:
GND: C1.2, C2.2, C3.2, POWER.1, T1.1, T2.1, T3.1
T1: C1.1, R1.2, T1.2
T2: C2.1, R2.2, T2.2
T3: C3.1, R3.2, T3.2
VCC: POWER.2, R1.1, R2.1, R3.1

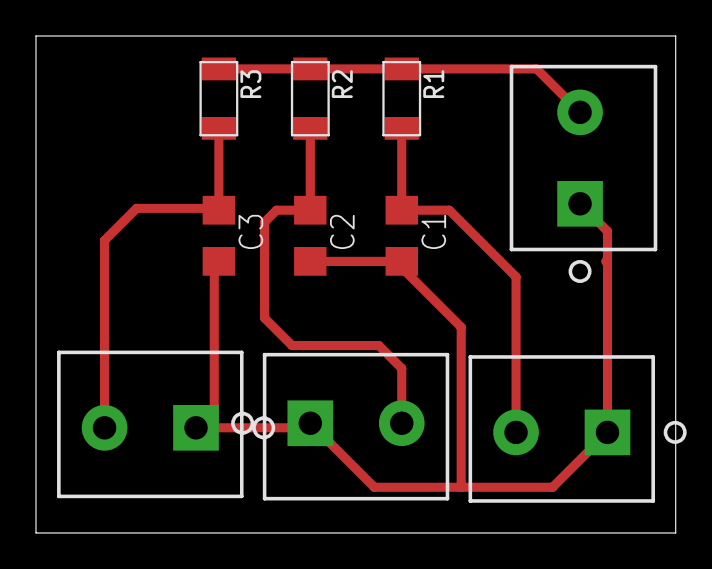
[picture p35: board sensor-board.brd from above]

Board: 2 copper layers, 35.5 x 27.6 mm, 10 parts (0 on the bottom side), 5 nets.

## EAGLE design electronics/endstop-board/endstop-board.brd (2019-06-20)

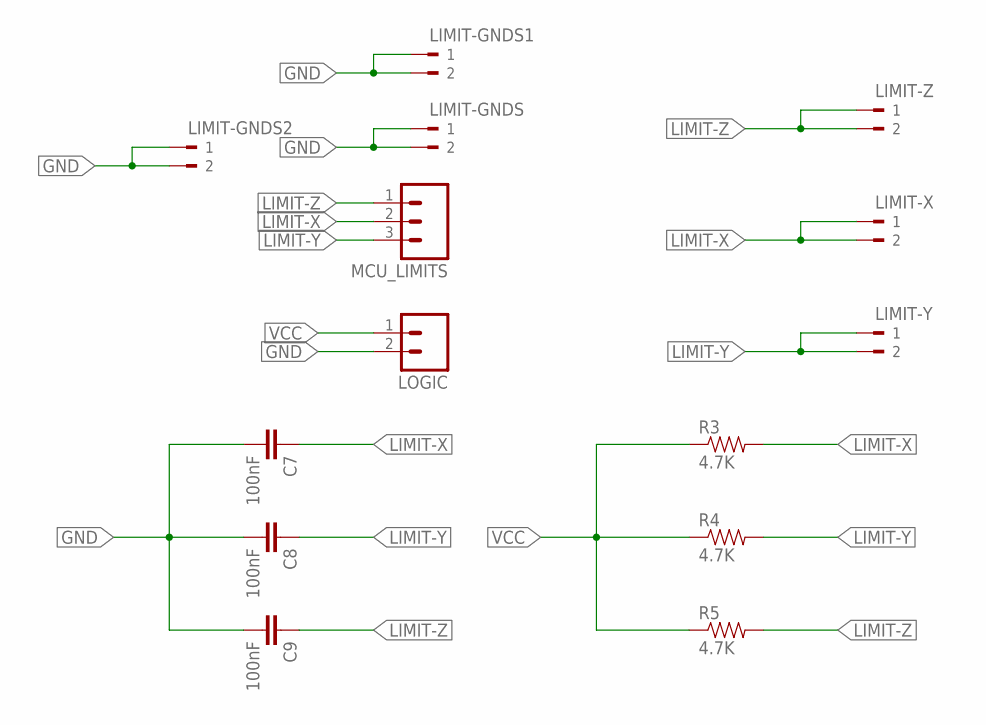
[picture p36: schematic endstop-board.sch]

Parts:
C7, C8, C9: 100nF; 1206
LIMIT-GNDS, LIMIT-GNDS1, LIMIT-GNDS2: PM5.08/2/90BLK; WEIDMULLER_PM5.08_2
LIMIT-X: PM5.08/2/90BLK; WEIDMULLER_PM5.08_2
LIMIT-Y: PM5.08/2/90BLK; WEIDMULLER_PM5.08_2
LIMIT-Z: PM5.08/2/90BLK; WEIDMULLER_PM5.08_2
LOGIC: M02; 02P
MCU_LIMITS: M03; 03P
R3, R4, R5: 4.7K; 1206

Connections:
GND: C7.2, C8.2, C9.2, LIMIT-GNDS.1, LIMIT-GNDS.2, LIMIT-GNDS1.1, LIMIT-GNDS1.2, LIMIT-GNDS2.1, LIMIT-GNDS2.2, LOGIC.2
LIMIT-X: C7.1, LIMIT-X.1, LIMIT-X.2, MCU_LIMITS.2, R3.2
LIMIT-Y: C8.1, LIMIT-Y.1, LIMIT-Y.2, MCU_LIMITS.3, R4.2
LIMIT-Z: C9.1, LIMIT-Z.1, LIMIT-Z.2, MCU_LIMITS.1, R5.2
VCC: LOGIC.1, R3.1, R4.1, R5.1

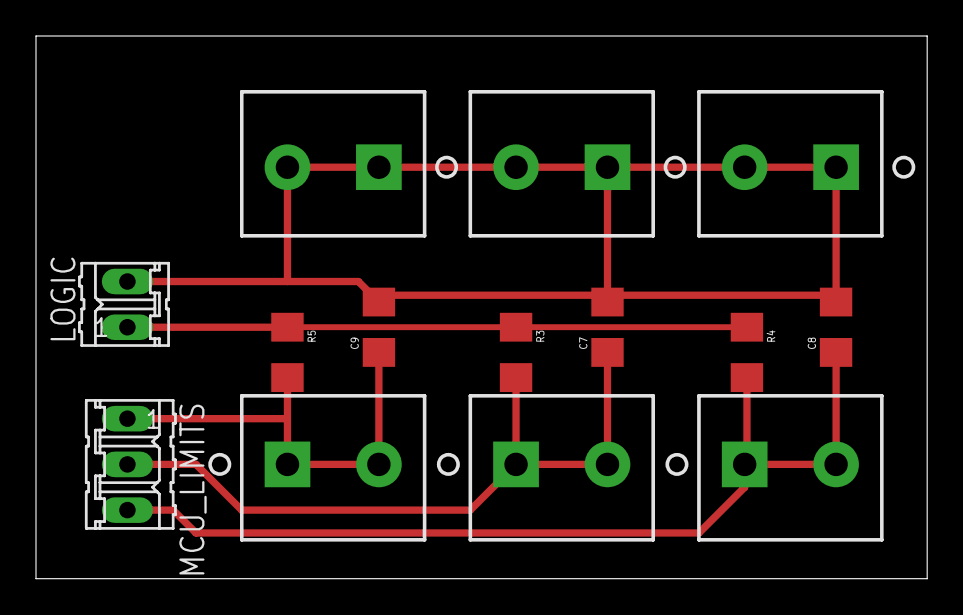
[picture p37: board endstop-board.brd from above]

Board: 2 copper layers, 49.5 x 30.1 mm, 14 parts (0 on the bottom side), 5 nets.

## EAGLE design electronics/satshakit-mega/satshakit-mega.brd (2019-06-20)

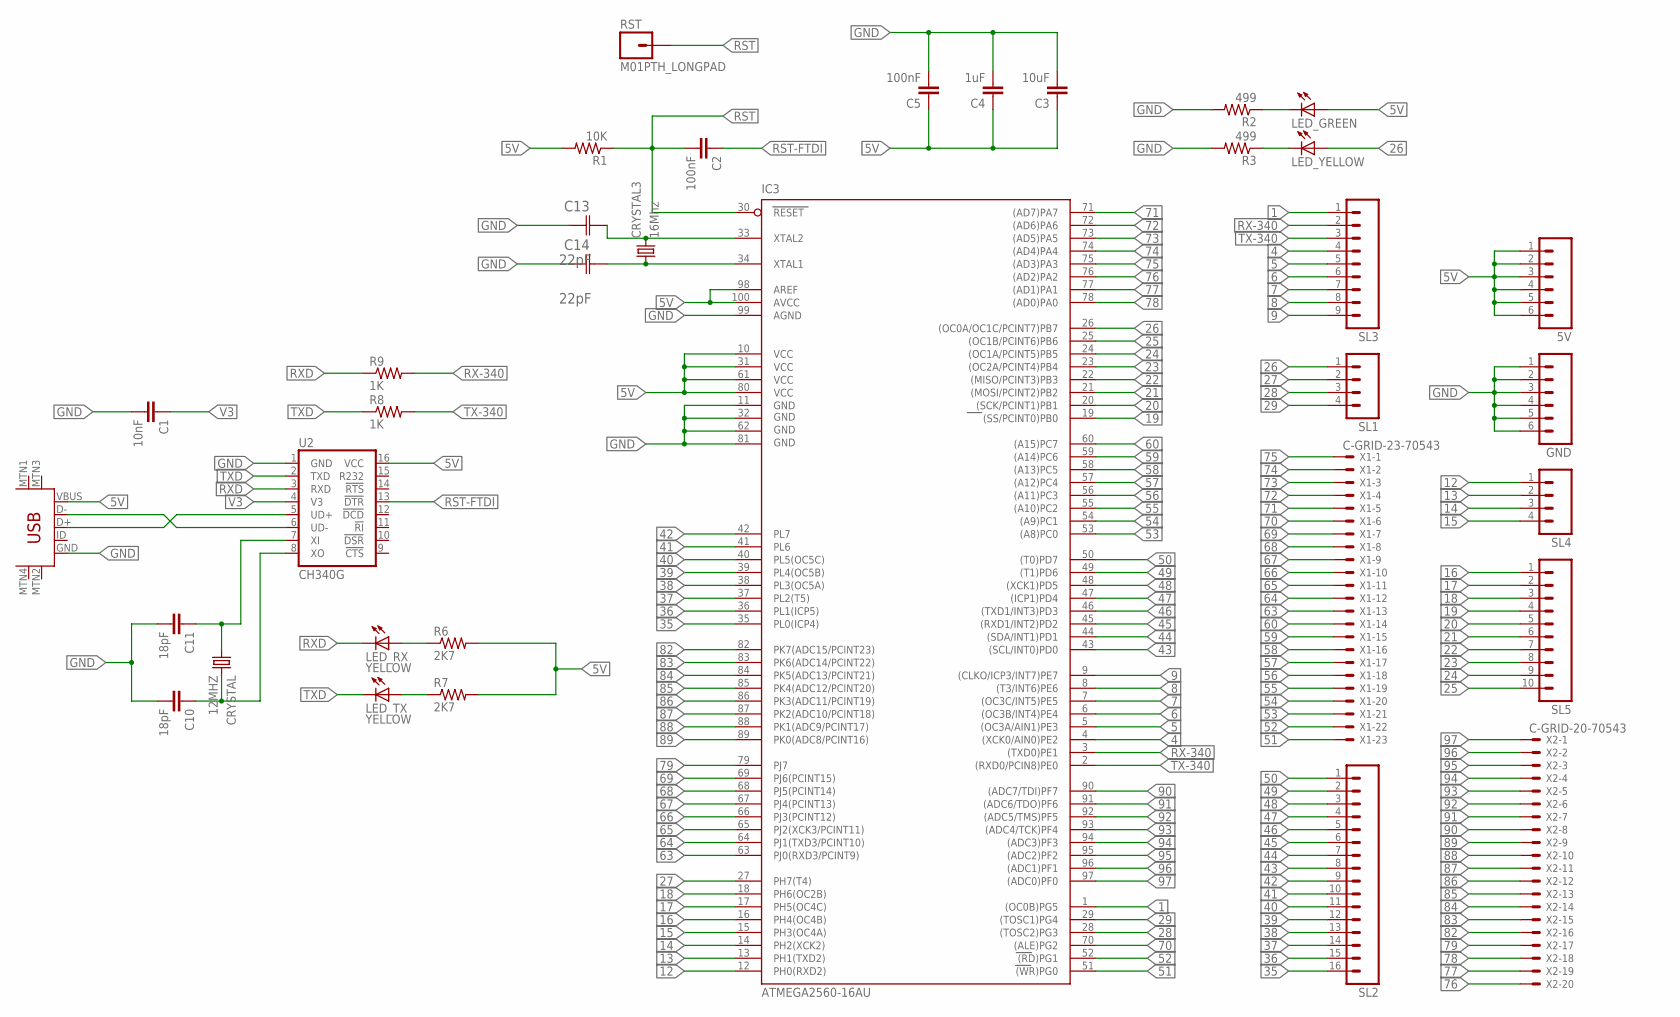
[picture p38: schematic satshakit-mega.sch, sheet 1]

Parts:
5V: M06; 06P
C1: 10nF; 1206
C2, C5: 100nF; 1206
C3: 10uF; 1206
C4: 1uF; 1206
C10, C11: 18pF; 1206
C13, C14: 22pF; CAPC3216X178N
CRYSTAL: 12MHZ; CSM-7X-DU
CRYSTAL3: 16Mhz; CSM-7X-DU
GND: M06; 06P
IC3: ATMEGA2560-16AU; TQFP100
LED_GREEN: LED1206; 1206
LED_RX: YELLOW; LED1206
LED_TX: YELLOW; LED1206
LED_YELLOW: LED1206; 1206
R1: 10K; R1206
R2, R3: 499; 1206
R6, R7: 2K7; R1206
R8, R9: 1K; R1206
RST: M01PTH_LONGPAD; 1X01_LONGPAD
SL1, SL4: M04; 04P
SL2: M16; 16P
SL3: M09; 09P
SL5: M10; 10P
U2: CH340G; SO016
U$7: USB-MINIB-5PIN; USB-MINIB
X1: C-GRID-23-70543; 70543-23
X2: C-GRID-20-70543; 70543-20

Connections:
1: IC3.1 ((OC0B)PG5), SL3.1
4: IC3.4 ((XCK0/AIN0)PE2), SL3.4
5: IC3.5 ((OC3A/AIN1)PE3), SL3.5
5V: 5V.1, 5V.2, 5V.3, 5V.4, 5V.5, 5V.6, C3.1, C4.1, C5.1, IC3.10 (VCC), IC3.31 (VCC1), IC3.61 (VCC2), IC3.80 (VCC3), IC3.98 (AREF), IC3.100 (AVCC), LED_GREEN.1 (A), R1.2, R6.2, R7.2, U2.16 (VCC), U$7.VBUS
6: IC3.6 ((OC3B/INT4)PE4), SL3.6
7: IC3.7 ((OC3C/INT5)PE5), SL3.7
8: IC3.8 ((T3/INT6)PE6), SL3.8
9: IC3.9 ((CLKO/ICP3/INT7)PE7), SL3.9
12: IC3.12 (PH0(RXD2)), SL4.1
13: IC3.13 (PH1(TXD2)), SL4.2
14: IC3.14 (PH2(XCK2)), SL4.3
15: IC3.15 (PH3(OC4A)), SL4.4
16: IC3.16 (PH4(OC4B)), SL5.1
17: IC3.17 (PH5(OC4C)), SL5.2
18: IC3.18 (PH6(OC2B)), SL5.3
19: IC3.19 ((SS/PCINT0)PB0), SL5.4
20: IC3.20 ((SCK/PCINT1)PB1), SL5.5
21: IC3.21 ((MOSI/PCINT2)PB2), SL5.6
22: IC3.22 ((MISO/PCINT3)PB3), SL5.7
23: IC3.23 ((OC2A/PCINT4)PB4), SL5.8
24: IC3.24 ((OC1A/PCINT5)PB5), SL5.9
25: IC3.25 ((OC1B/PCINT6)PB6), SL5.10
26: IC3.26 ((OC0A/OC1C/PCINT7)PB7), LED_YELLOW.1 (A), SL1.1
27: IC3.27 (PH7(T4)), SL1.2
28: IC3.28 ((TOSC2)PG3), SL1.3
29: IC3.29 ((TOSC1)PG4), SL1.4
35: IC3.35 (PL0(ICP4)), SL2.16
36: IC3.36 (PL1(ICP5)), SL2.15
37: IC3.37 (PL2(T5)), SL2.14
38: IC3.38 (PL3(OC5A)), SL2.13
39: IC3.39 (PL4(OC5B)), SL2.12
40: IC3.40 (PL5(OC5C)), SL2.11
41: IC3.41 (PL6), SL2.10
42: IC3.42 (PL7), SL2.9
43: IC3.43 ((SCL/INT0)PD0), SL2.8
44: IC3.44 ((SDA/INT1)PD1), SL2.7
45: IC3.45 ((RXD1/INT2)PD2), SL2.6
46: IC3.46 ((TXD1/INT3)PD3), SL2.5
47: IC3.47 ((ICP1)PD4), SL2.4
48: IC3.48 ((XCK1)PD5), SL2.3
49: IC3.49 ((T1)PD6), SL2.2
50: IC3.50 ((T0)PD7), SL2.1
51: IC3.51 ((WR)PG0), X1.23
52: IC3.52 ((RD)PG1), X1.22
53: IC3.53 ((A8)PC0), X1.21
54: IC3.54 ((A9)PC1), X1.20
55: IC3.55 ((A10)PC2), X1.19
56: IC3.56 ((A11)PC3), X1.18
57: IC3.57 ((A12)PC4), X1.17
58: IC3.58 ((A13)PC5), X1.16
59: IC3.59 ((A14)PC6), X1.15
60: IC3.60 ((A15)PC7), X1.14
63: IC3.63 (PJ0(RXD3/PCINT9)), X1.13
64: IC3.64 (PJ1(TXD3/PCINT10)), X1.12
65: IC3.65 (PJ2(XCK3/PCINT11)), X1.11
66: IC3.66 (PJ3(PCINT12)), X1.10
67: IC3.67 (PJ4(PCINT13)), X1.9
68: IC3.68 (PJ5(PCINT14)), X1.8
69: IC3.69 (PJ6(PCINT15)), X1.7
70: IC3.70 ((ALE)PG2), X1.6
71: IC3.71 ((AD7)PA7), X1.5
72: IC3.72 ((AD6)PA6), X1.4
73: IC3.73 ((AD5)PA5), X1.3
74: IC3.74 ((AD4)PA4), X1.2
75: IC3.75 ((AD3)PA3), X1.1
76: IC3.76 ((AD2)PA2), X2.20
77: IC3.77 ((AD1)PA1), X2.19
78: IC3.78 ((AD0)PA0), X2.18
79: IC3.79 (PJ7), X2.17
82: IC3.82 (PK7(ADC15/PCINT23)), X2.16
83: IC3.83 (PK6(ADC14/PCINT22)), X2.15
84: IC3.84 (PK5(ADC13/PCINT21)), X2.14
85: IC3.85 (PK4(ADC12/PCINT20)), X2.13
86: IC3.86 (PK3(ADC11/PCINT19)), X2.12
87: IC3.87 (PK2(ADC10/PCINT18)), X2.11
88: IC3.88 (PK1(ADC9/PCINT17)), X2.10
89: IC3.89 (PK0(ADC8/PCINT16)), X2.9
90: IC3.90 ((ADC7/TDI)PF7), X2.8
91: IC3.91 ((ADC6/TDO)PF6), X2.7
92: IC3.92 ((ADC5/TMS)PF5), X2.6
93: IC3.93 ((ADC4/TCK)PF4), X2.5
94: IC3.94 ((ADC3)PF3), X2.4
95: IC3.95 ((ADC2)PF2), X2.3
96: IC3.96 ((ADC1)PF1), X2.2
97: IC3.97 ((ADC0)PF0), X2.1
GND: C1.2, C3.2, C4.2, C5.2, C10.2, C11.2, C13.1 (C1), C14.1 (C1), GND.1, GND.2, GND.3, GND.4, GND.5, GND.6, IC3.11 (GND), IC3.32 (GND1), IC3.62 (GND2), IC3.81 (GND3), IC3.99 (AGND), R2.2, R3.2, U2.1 (GND), U$7.GND
unnamed: U2.5 (UD+), U$7.D+
unnamed: LED_RX.1 (A), R6.1
unnamed: U2.6 (UD-), U$7.D-
unnamed: C14.2 (C2), CRYSTAL3.1, IC3.34 (XTAL1)
unnamed: C13.2 (C2), CRYSTAL3.2, IC3.33 (XTAL2)
unnamed: LED_YELLOW.2 (C), R3.1
unnamed: LED_TX.1 (A), R7.1
unnamed: LED_GREEN.2 (C), R2.1
OSC_IN: C10.1, CRYSTAL.2, U2.8 (XO)
OSC_OUT: C11.1, CRYSTAL.1, U2.7 (XI)
RST: C2.2, IC3.30 (RESET), R1.1, RST.1
RST-FTDI: C2.1, U2.13 (!DTR)
RX-340: IC3.3 ((TXD0)PE1), R9.2, SL3.2
RXD: LED_RX.2 (C), R9.1, U2.3 (RXD)
TX-340: IC3.2 ((RXD0/PCIN8)PE0), R8.2, SL3.3
TXD: LED_TX.2 (C), R8.1, U2.2 (TXD)
V3: C1.1, U2.4 (V3)

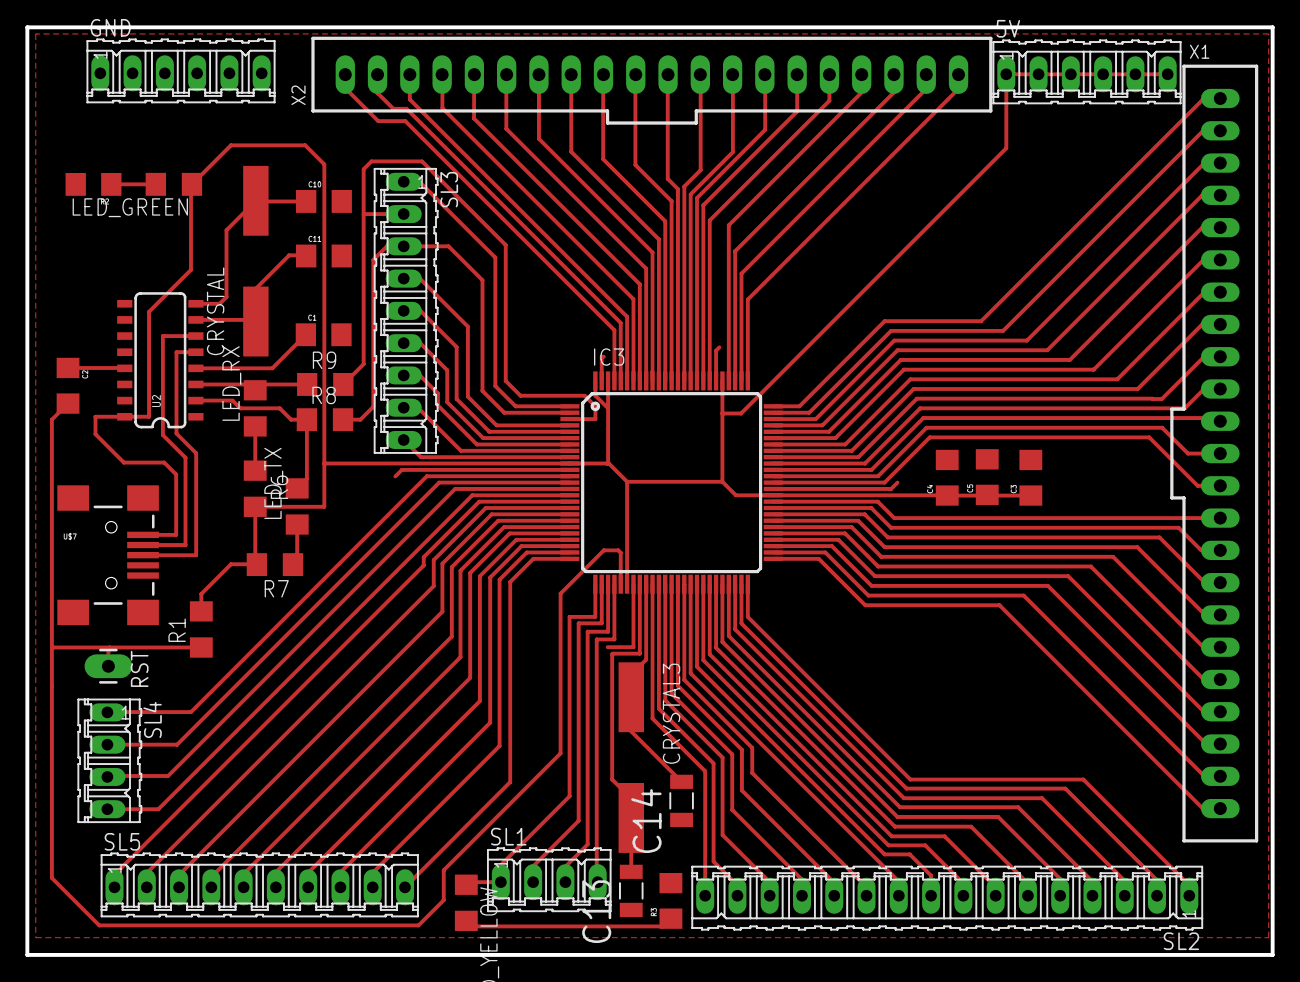
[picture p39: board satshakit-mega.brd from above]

Board: 2 copper layers, 98.0 x 73.0 mm, 35 parts (0 on the bottom side), 103 nets.

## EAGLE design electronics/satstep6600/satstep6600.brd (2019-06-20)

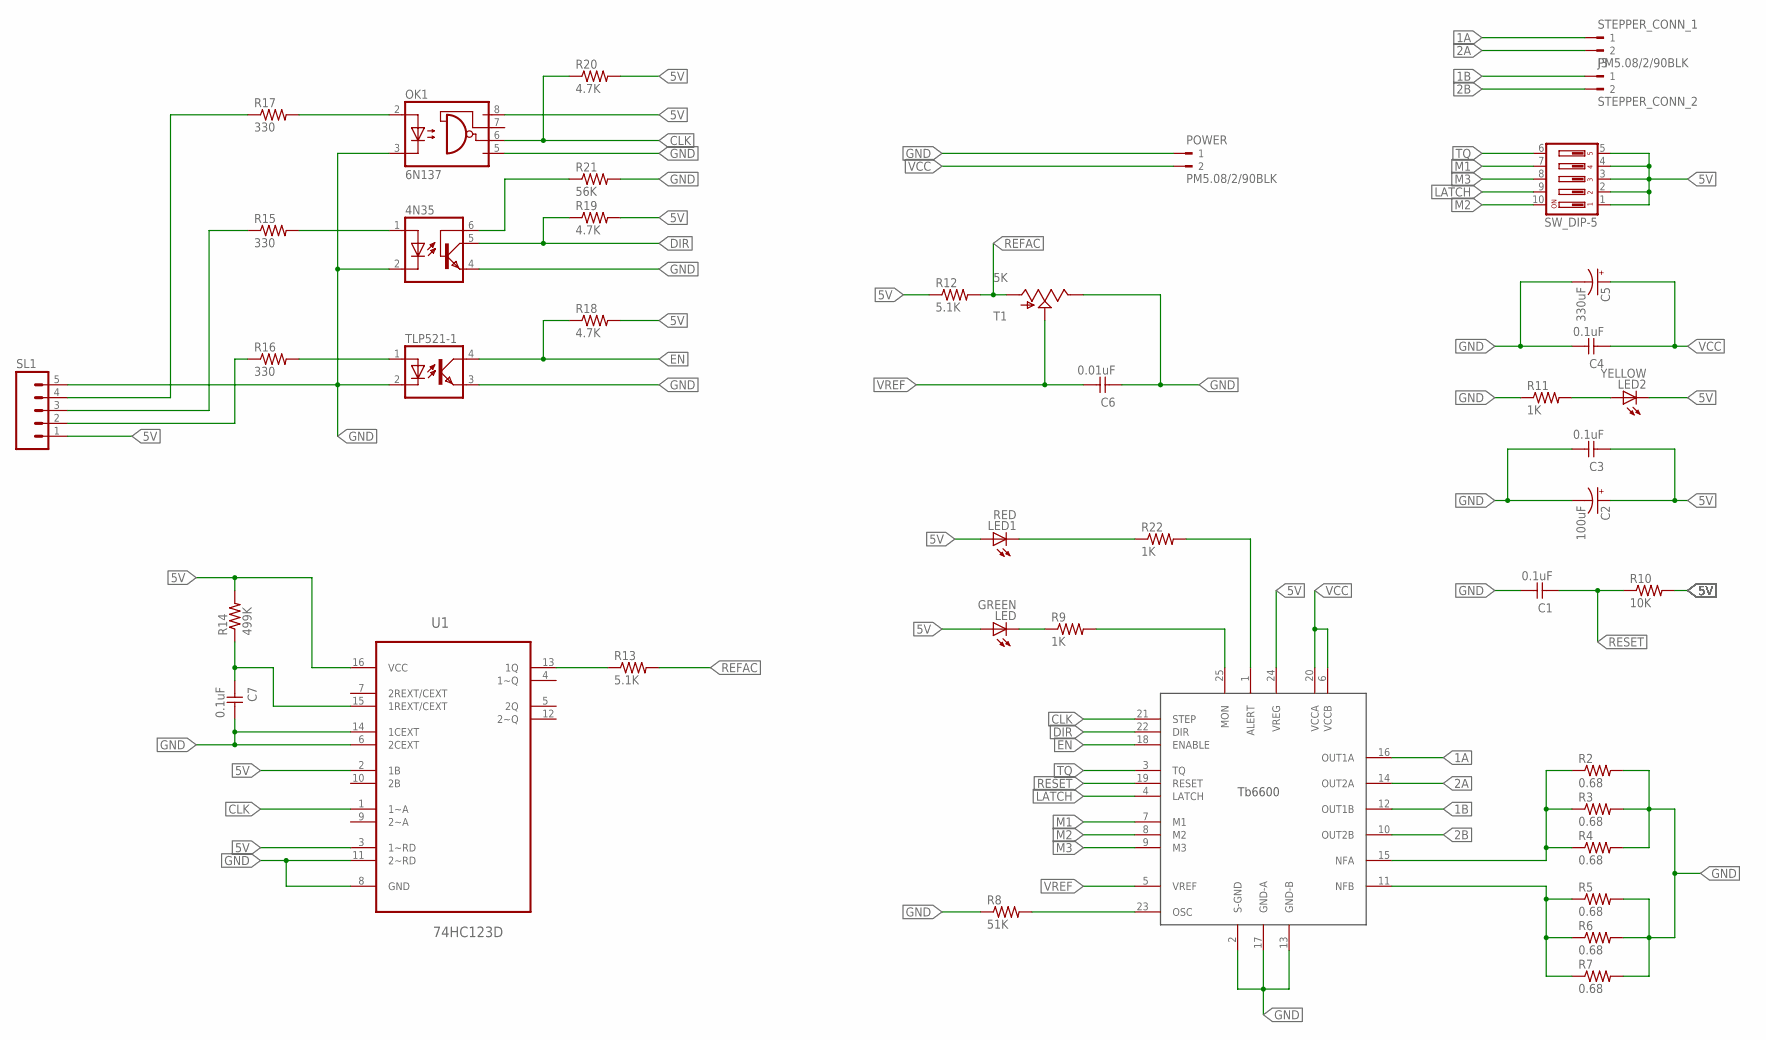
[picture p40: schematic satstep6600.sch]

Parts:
4N35: 4N35; DIL06
C1, C3, C4, C7: 0.1uF; 1206
C2: 100uF; PANASONIC_C
C5: 330uF; CPOL-RADIAL-1000UF-63V
C6: 0.01uF; 1206
J3: STEPPER_CONN_2; WEIDMULLER_PM5.08_2
LED: GREEN; 1206
LED1: RED; 1206
LED2: YELLOW; 1206
OK1: 6N137; DIL08
POWER: PM5.08/2/90BLK; WEIDMULLER_PM5.08_2
R2, R3, R4, R5, R6, R7: 0.68; 2512
R8: 51K; R1206
R9, R11, R22: 1K; R1206
R10: 10K; R1206
R12, R13: 5.1K; R1206
R14: 499K; R1206
R15, R16, R17: 330; R1206
R18, R19, R20: 4.7K; R1206
R21: 56K; R1206
SL1: M05; 05P
STEPPER_CONN_1: PM5.08/2/90BLK; WEIDMULLER_PM5.08_2
SW_DIP-5: SD4-05
T1: 5K; TS53YL104MR10_TRIMMER
TLP521-1: PC817; DIL04
U1: 74HC123D; SOIC127P600X175-16N
U$1: TB6600HG; P-HZIP25-1.00G

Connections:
1A: STEPPER_CONN_1.1, U$1.16 (OUT1A)
1B: J3.1, U$1.12 (OUT1B)
2A: STEPPER_CONN_1.2, U$1.14 (OUT2A)
2B: J3.2, U$1.10 (OUT2B)
5V: C2.+, C3.1, LED.1 (A), LED1.1 (A), LED2.2 (C), OK1.8 (VCC), R10.2, R12.1, R14.2, R18.2, R19.2, R20.2, SL1.1, SW_DIP-5.1, SW_DIP-5.2, SW_DIP-5.3, SW_DIP-5.4, SW_DIP-5.5, U1.2 (1B), U1.3 (1~RD), U1.16 (VCC), U$1.24 (VREG)
ALERT: R22.2, U$1.1 (ALERT)
CLK: OK1.6 (VO), R20.1, U1.1 (1~A), U$1.21 (STEP)
DIR: 4N35.5 (COL), R19.1, U$1.22 (DIR)
EN: R18.1, TLP521-1.4 (COL), U$1.18 (ENABLE)
GND: 4N35.2 (C), 4N35.4 (EMI), C1.2, C2.-, C3.2, C4.2, C5.2 (-), C6.1, C7.2, OK1.3 (C), OK1.5 (GND), POWER.1, R2.2, R3.2, R4.2, R5.2, R6.2, R7.2, R8.1, R11.1, R21.2, SL1.5, T1.P$2 (E), TLP521-1.2 (C), TLP521-1.3 (EMIT), U1.6 (2CEXT), U1.8 (GND), U1.11 (2~RD), U1.14 (1CEXT), U$1.2 (S-GND), U$1.13 (GND-B), U$1.17 (GND-A)
LATCH: SW_DIP-5.9, U$1.4 (LATCH)
M1: SW_DIP-5.7, U$1.7 (M1)
M2: SW_DIP-5.10, U$1.8 (M2)
M3: SW_DIP-5.8, U$1.9 (M3)
unnamed: R5.1, R6.1, R7.1, U$1.11 (NFB)
unnamed: R8.2, U$1.23 (OSC)
unnamed: LED.2 (C), R9.1
unnamed: R2.1, R3.1, R4.1, U$1.15 (NFA)
unnamed: LED1.2 (C), R22.1
unnamed: LED2.1 (A), R11.2
unnamed: R13.1, U1.13 (1Q)
unnamed: C7.1, R14.1, U1.15 (1REXT/CEXT)
unnamed: R16.2, TLP521-1.1 (A)
unnamed: 4N35.1 (A), R15.2
unnamed: OK1.2 (A), R17.2
unnamed: 4N35.6 (BAS), R21.1
unnamed: R16.1, SL1.2
unnamed: R15.1, SL1.3
unnamed: R17.1, SL1.4
unnamed: R9.2, U$1.25 (MON)
REFAC: R12.2, R13.2, T1.P$3 (A)
RESET: C1.1, R10.1, U$1.19 (RESET)
TQ: SW_DIP-5.6, U$1.3 (TQ)
VCC: C4.1, C5.1 (+), POWER.2, U$1.6 (VCCB), U$1.20 (VCCA)
VREF: C6.2, T1.P$1 (S), U$1.5 (VREF)

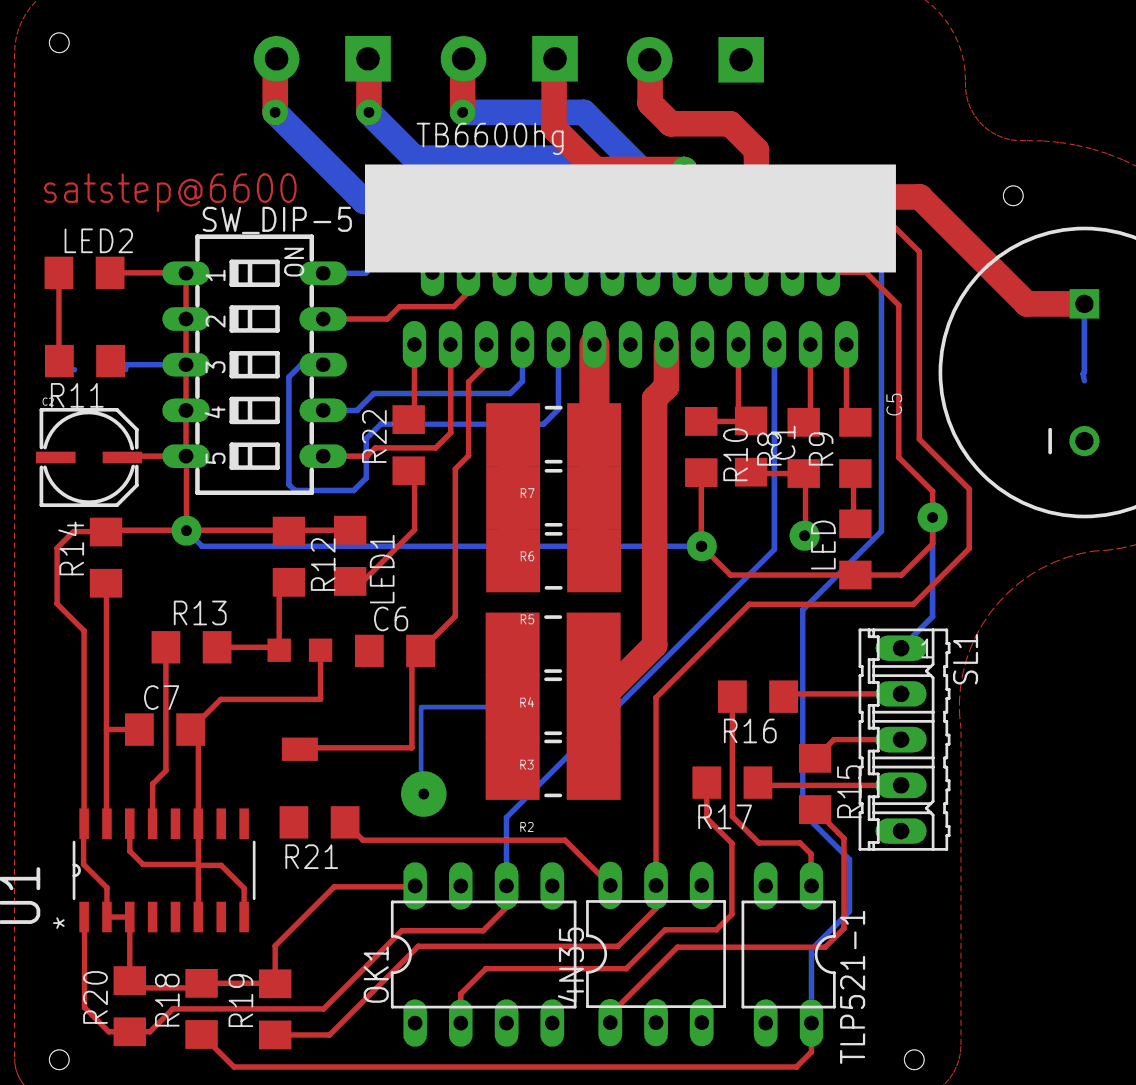
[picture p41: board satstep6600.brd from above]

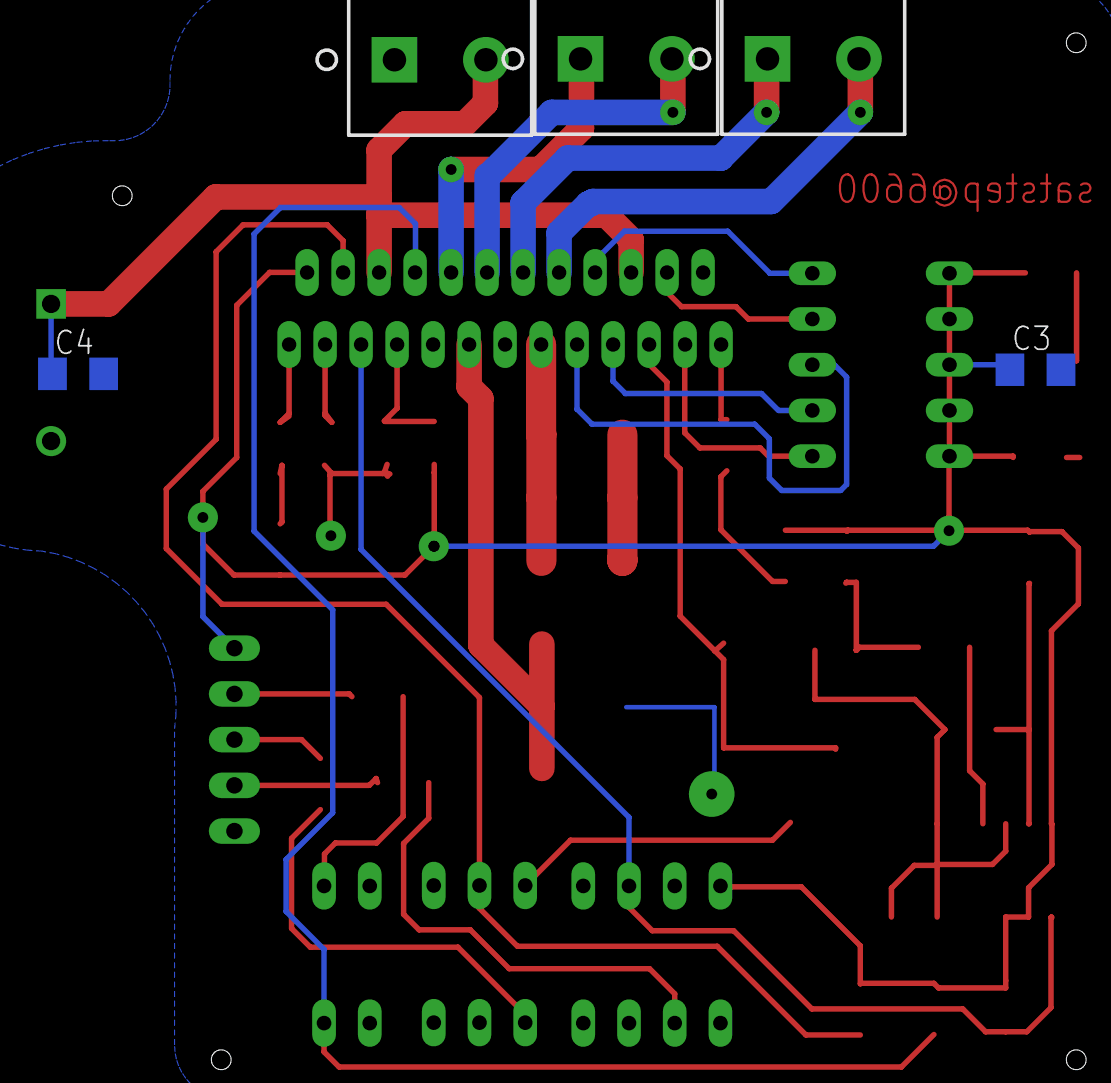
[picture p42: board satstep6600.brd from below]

Board: 2 copper layers, 42 parts (5 on the bottom side), 35 nets.

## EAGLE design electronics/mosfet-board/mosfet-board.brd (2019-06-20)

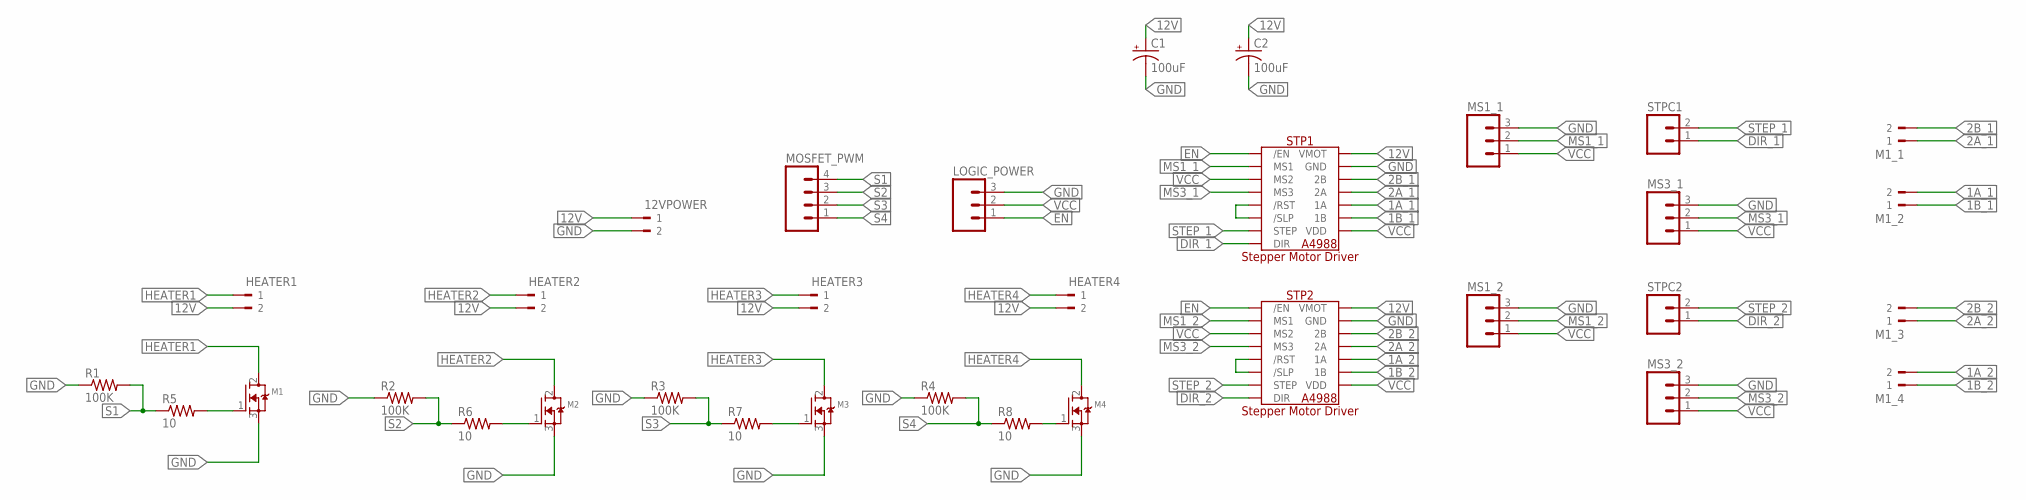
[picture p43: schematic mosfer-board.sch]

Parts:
12VPOWER: PM5.08/2/90BLK; WEIDMULLER_PM5.08_2
C1, C2: 100uF; CPOL-RADIAL-2.5MM-6.5MM
HEATER1, HEATER2, HEATER3, HEATER4: PM5.08/2/90BLK; WEIDMULLER_PM5.08_2
LOGIC_POWER: M03; 03P
M1, M2, M3, M4: MOSFET-NGDS_TO220V; TO220V
M1_1, M1_2, M1_3, M1_4: PM5.08/2/90BLK; WEIDMULLER_PM5.08_2
MOSFET_PWM: M04; 04P
MS1_1, MS1_2, MS3_1, MS3_2: M03; 03P
R1, R2, R3, R4: 100K; R1206FAB
R5, R6, R7, R8: 10; R1206FAB
STP1, STP2: A4988_STEP
STPC1, STPC2: M02; 02P

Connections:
1A_1: M1_2.2, STP1.1A
1A_2: M1_4.2, STP2.1A
1B_1: M1_2.1, STP1.1B
1B_2: M1_4.1, STP2.1B
2A_1: M1_1.1, STP1.2A
2A_2: M1_3.1, STP2.2A
2B_1: M1_1.2, STP1.2B
2B_2: M1_3.2, STP2.2B
12V: 12VPOWER.1, C1.1 (+), C2.1 (+), HEATER1.2, HEATER2.2, HEATER3.2, HEATER4.2, STP1.VMOT, STP2.VMOT
DIR_1: STP1.DIR, STPC1.1
DIR_2: STP2.DIR, STPC2.1
EN: LOGIC_POWER.1, STP1./EN, STP2./EN
GND: 12VPOWER.2, C1.2 (-), C2.2 (-), LOGIC_POWER.3, M1.3 (S), M2.3 (S), M3.3 (S), M4.3 (S), MS1_1.3, MS1_2.3, MS3_1.3, MS3_2.3, R1.1, R2.1, R3.1, R4.1, STP1.GND, STP1.GND2 (GND), STP2.GND, STP2.GND2 (GND)
HEATER1: HEATER1.1, M1.2 (D)
HEATER2: HEATER2.1, M2.2 (D)
HEATER3: HEATER3.1, M3.2 (D)
HEATER4: HEATER4.1, M4.2 (D)
MS1_1: MS1_1.2, STP1.MS1
MS1_2: MS1_2.2, STP2.MS1
MS3_1: MS3_1.2, STP1.MS3
MS3_2: MS3_2.2, STP2.MS3
unnamed: STP1./RST, STP1./SLP
unnamed: STP2./RST, STP2./SLP
unnamed: M3.1 (G), R7.2
unnamed: M2.1 (G), R6.2
unnamed: M1.1 (G), R5.2
unnamed: M4.1 (G), R8.2
S1: MOSFET_PWM.4, R1.2, R5.1
S2: MOSFET_PWM.3, R2.2, R6.1
S3: MOSFET_PWM.2, R3.2, R7.1
S4: MOSFET_PWM.1, R4.2, R8.1
STEP_1: STP1.STEP, STPC1.2
STEP_2: STP2.STEP, STPC2.2
VCC: LOGIC_POWER.2, MS1_1.1, MS1_2.1, MS3_1.1, MS3_2.1, STP1.MS2, STP1.VDD, STP2.MS2, STP2.VDD

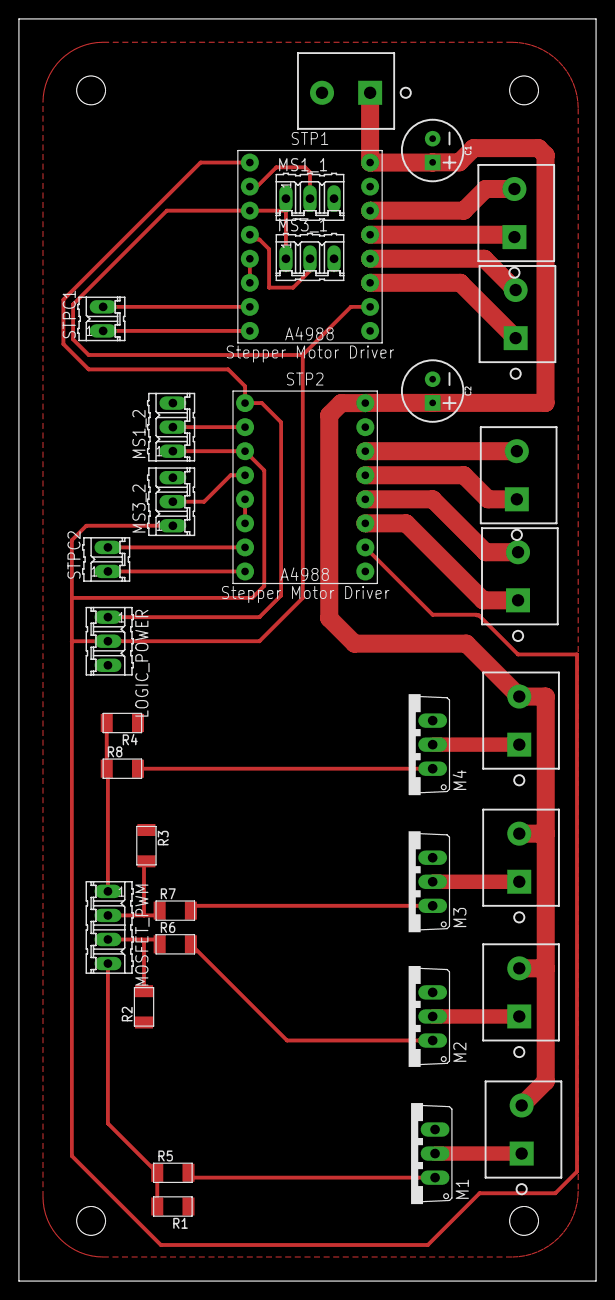
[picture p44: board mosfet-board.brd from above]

Board: 2 copper layers, 60.9 x 133.3 mm, 33 parts (0 on the bottom side), 34 nets.

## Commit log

2019-07-05 updated bom, cad file, README
2019-07-05 removed html bom
2019-07-06 added housing description
2019-07-06 added real assembly pics
2019-07-06 updated BOM

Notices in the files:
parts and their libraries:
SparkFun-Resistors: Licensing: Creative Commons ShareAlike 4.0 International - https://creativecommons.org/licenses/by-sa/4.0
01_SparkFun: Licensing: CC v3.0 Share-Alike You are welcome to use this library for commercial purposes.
